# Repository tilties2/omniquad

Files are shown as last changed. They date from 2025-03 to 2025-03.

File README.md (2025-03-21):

# OmniQuad Design

This folder contains the files to build the OmniQuad presented in the paper "Design and Control of an Omnidirectional Aerial Robot with 4DoF Haptic Joystick for Physical Interaction". The objective is to improve reproducibility in robotics, by providing an haptic remote controller for a telemanipulation system.

Freeflight           |  Physical interaction
:-------------------------:|:-------------------------:
  |  

## Overview

Omnidirectional platforms are complexe machines with a lot of components, requiring substantial maintenance due to the complexity of their systems and current manufacturing techniques. Here we propose an optimized robot design with a reduced number of parts and 3D printed parts. We first present the design of the tilting arm, then we show how it is mounted on the full robot.

## OmniQuad Tilting Arm

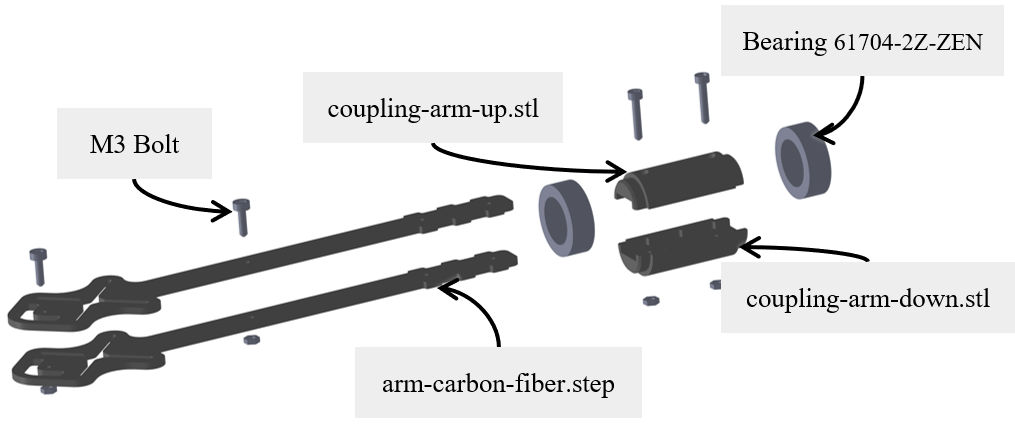
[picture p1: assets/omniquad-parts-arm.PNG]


The tilting platform arm proposes to simplify the rotor mounting. Instead of using tubular shape, here we propose to directly link the motor to a two sheets of 3mm carbon fiber. These CNC cut arms are attached with bolts, and their shape is presented bellow.

### 3D print and CNC cut

The revolut joint is done with two coupling parts that link the carbon fiber arm. The experience showed that PETG was the material to use, combining ease to manufacture and resilience:

- [Coupling arm up](parts/coupling-arm-up.stl) x 4
- [Coulping arm down](parts/coupling-arm-down.stl) x 4
- [Arm carbon fiber](parts/arm-carbon-fiber.step) x 8

### Others

The previously presented 3D printed parts clamp the carbon fiber sheets while ensuring support for the bearing. The servo actuators are attached to this coupling arm mechanism.

- 61704-2Z-ZEN bearings x 8
- M3 L25 bolts x 8
- M3 L12 bolts x 8

## OmniQuad full

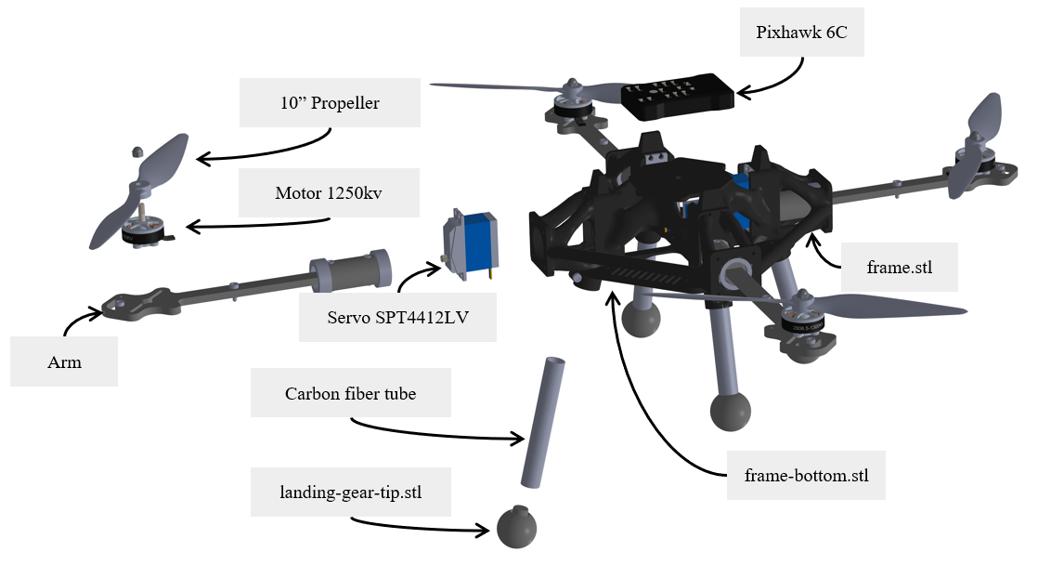
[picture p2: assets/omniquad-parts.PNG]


The robot chassis is the core component. The design we propose reduces the overall wheight of the robot while keeping rigidity against internal stress. The other parts are all attach around it.

### Upper part

Different materials have been tested, and the tough PETG is the one keeping a certain rigidity with resonable resilience to impacts. The frame links the arms that are secured with some caps. The latters are screwed into the frame and press the arm to lock it firmly againt the servo motors.

- [Frame](parts/frame.stl)
- [Cap](parts/cap-arm.stl) x 4
- M3 L10 screws x 16
- SPT4412LV servo  x 4
- M3 L8 screws x 16

### Bottom part

After having installed the tilting mechanism, the ESC can be mounted on the bottom of the frame. This has to be screwed to close the robot frame, while the gears made with the tubes of carbon fiber close the structure. Flexible tip, printed out of TPU, are mounted to the other end of the rod

- [Bottom frame](parts/frame-bottom.stl)
- [Tip landing gear](parts/landing-gear-tip.stl)

### Electronics and other

Here we use a Pixhawk flight controller to flash our custom version of [PX4](https://github.com/tilties2/PX4-OmniQuad). Propellers have to be 10" and motors of 1250-1300kv

- Pixhawk 6C
- 10x4.5 propellers x 4
- iFlight XING2 2809 1250KV brushless motors x 4

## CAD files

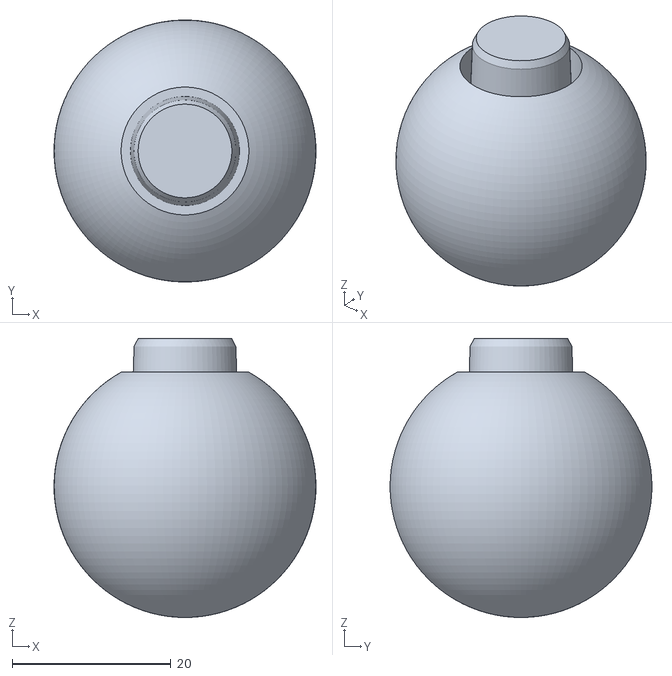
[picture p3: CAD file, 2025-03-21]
parts/landing-gear-tip.stl
33.0 x 33.0 x 35.1

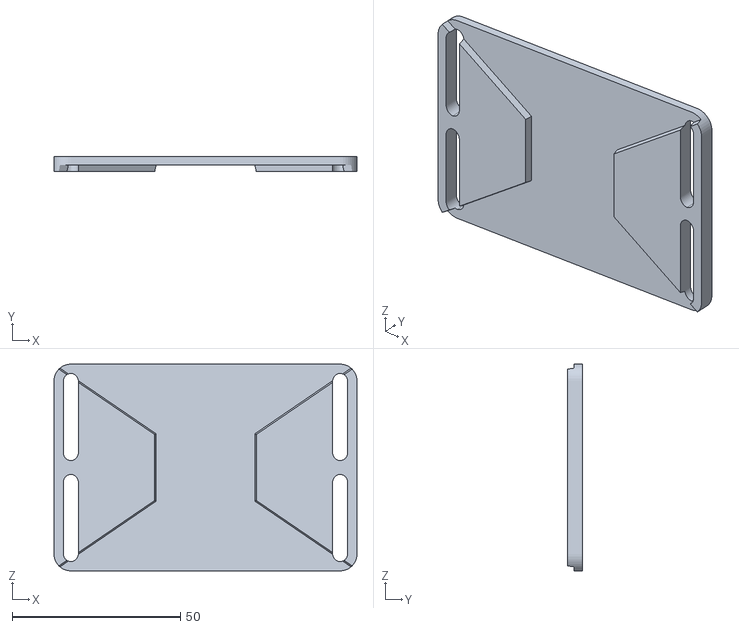
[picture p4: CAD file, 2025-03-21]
parts/battery-spacer.stl
90.0 x 4.50 x 61.4

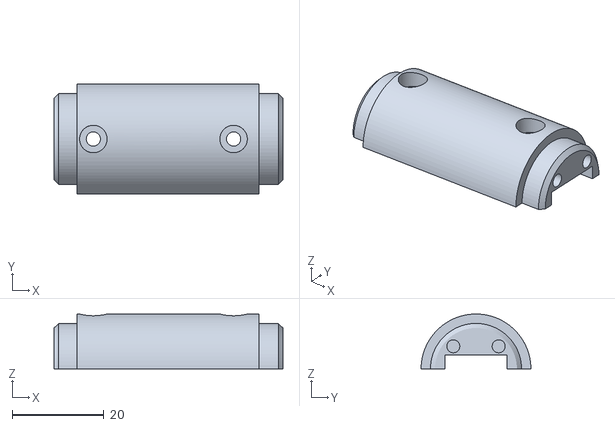
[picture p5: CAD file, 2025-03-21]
parts/coupling-arm-down.stl
50.0 x 24.0 x 12.0

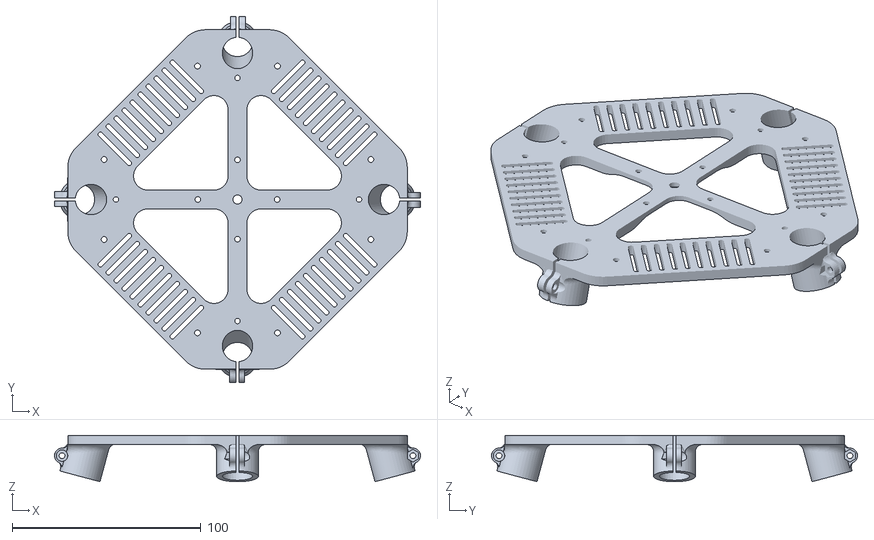
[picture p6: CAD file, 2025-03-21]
parts/frame-bottom.stl
194.0 x 194.0 x 24.6

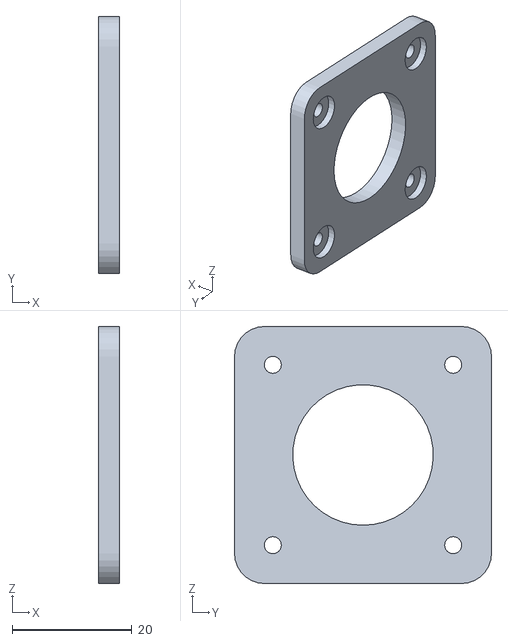
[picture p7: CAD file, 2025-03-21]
parts/cap-arm.stl
3.50 x 43.0 x 43.0

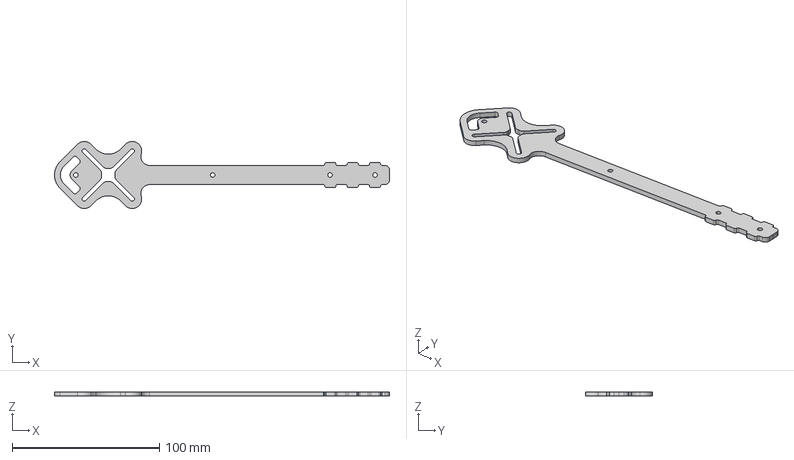
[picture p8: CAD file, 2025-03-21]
parts/arm-carbon-fiber.step
227.6 x 45.5 x 3.00 mm

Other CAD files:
parts/coupling-arm-up.stl
